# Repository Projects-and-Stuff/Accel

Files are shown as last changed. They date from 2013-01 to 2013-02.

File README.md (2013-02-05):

# Accel #
#### A 50cm diameter continuous pulsed solenoid for testing control and feedback algorithms ####
#### This can be considered to be a sort of infinite controlled coil gun or a miniature circular mass-driver ####
---

*File Structure*

* ./Firmware/ --> Firmware for the project (Written in C Utilizing AVR Studio 6)
* ./Hardware/ --> OpenSCAD part file and .STL file
* ./ElecHardware/ --> Kicad Projects for Accel
* ./GerberOutput/ --> The latest PCB Gerber Files for manufacture
* ./Notes/ --> Project Notes, BOM, and Research

---

Additional information, research, and notes can be found at http://www.projectsandstuff.com, or email us at support@projectsandstuff.com

Let us know if you fork and make improvements. We'd be glad to consider merges that improve this project.

---

Updates can be found in the Project Log, in the Notes folder

---

CURRENT AUTHORS:

> [Jack Linke](http://www.jacklinke.com)
jacklinke@gmail.com

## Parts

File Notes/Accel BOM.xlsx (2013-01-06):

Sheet: Control Board
Bill of Materials - Accel - Control Board |  |  |  |  |  |  |  |  |  | # of boards goal: | 1
Projects and Stuff LLC - http://www.projectsandstuff.com
Total BOM Parts Cost: | $1.23
Description | Mfg Part # | Package | KiCad Footprint | Default Supplier | Supplier On Hand | Qty per board | Total Qty Needed | Price per part at Qty | Total Price | Notes | Part References
Shift Register, 8-bit | MC74HC165ADG (http://www.digikey.com/product-detail/en/MC74HC165ADG/MC74HC165ADGOS-ND/1479887) | 16-SOIC |  | DigiKey | 8387 | 3 | 3 | $0.41000 | $1.23
 |  |  |  |  |  |  | 0 |  | $0.00
 |  |  |  |  |  |  | 0 |  | $0.00
 |  |  |  |  |  |  | 0 |  | $0.00
 |  |  |  |  |  |  | 0 |  | $0.00
 |  |  |  |  |  |  | 0 |  | $0.00
 |  |  |  |  |  |  | 0 |  | $0.00
 |  |  |  |  |  |  | 0 |  | $0.00
 |  |  |  |  |  |  | 0 |  | $0.00
 |  |  |  |  |  |  | 0 |  | $0.00
 |  |  |  |  |  |  | 0 |  | $0.00
 |  |  |  |  |  |  | 0 |  | $0.00
 |  |  |  |  |  |  | 0 |  | $0.00
 |  |  |  |  |  |  | 0 |  | $0.00
 |  |  |  |  |  |  | 0 |  | $0.00
 |  |  |  |  |  |  | 0 |  | $0.00
 |  |  |  |  |  |  | 0 |  | $0.00
 |  |  |  |  |  |  | 0 |  | $0.00
 |  |  |  |  |  |  | 0 |  | $0.00
 |  |  |  |  |  |  | 0 |  | $0.00
 |  |  |  |  |  |  | 0 |  | $0.00
 |  |  |  |  |  |  | 0 |  | $0.00
 |  |  |  |  |  |  | 0 |  | $0.00
 |  |  |  |  |  |  | 0 |  | $0.00
 |  |  |  |  |  |  | 0 |  | $0.00
 |  |  |  |  |  |  | 0 |  | $0.00
 |  |  |  |  |  |  | 0 |  | $0.00
 |  |  |  |  |  |  | 0 |  | $0.00
 |  |  |  |  |  |  | 0 |  | $0.00
 |  |  |  |  |  |  | 0 |  | $0.00
 |  |  |  |  |  |  | 0 |  | $0.00
 |  |  |  |  |  |  | 0 |  | $0.00
 |  |  |  |  |  |  | 0 |  | $0.00
 |  |  |  |  |  |  | 0 |  | $0.00
 |  |  |  |  |  |  | 0 |  | $0.00
 |  |  |  |  |  |  | 0 |  | $0.00
 |  |  |  |  |  |  | 0 |  | $0.00
 |  |  |  |  |  |  | 0 |  | $0.00
 |  |  |  |  |  |  | 0 |  | $0.00
 |  |  |  |  |  |  | 0 |  | $0.00
 |  |  |  |  |  |  | 0 |  | $0.00
 |  |  |  |  |  |  | 0 |  | $0.00
 |  |  |  |  |  |  | 0 |  | $0.00
 |  |  |  |  |  |  | 0 |  | $0.00
 |  |  |  |  |  |  | 0 |  | $0.00
 |  |  |  |  |  |  | 0 |  | $0.00
 |  |  |  |  |  |  | 0 |  | $0.00
 |  |  |  |  |  |  | 0 |  | $0.00
 |  |  |  |  |  |  | 0 |  | $0.00
 |  |  |  |  |  |  | 0 |  | $0.00
 |  |  |  |  |  |  | 0 |  | $0.00
 |  |  |  |  |  |  | 0 |  | $0.00
 |  |  |  |  |  |  | 0 |  | $0.00
 |  |  |  |  |  |  | 0 |  | $0.00
 |  |  |  |  |  |  | 0 |  | $0.00
 |  |  |  |  |  |  | 0 |  | $0.00
 |  |  |  |  |  |  | 0 |  | $0.00
 |  |  |  |  |  |  | 0 |  | $0.00
 |  |  |  |  |  |  | 0 |  | $0.00
 |  |  |  |  |  |  | 0 |  | $0.00
 |  |  |  |  |  |  | 0 |  | $0.00
 |  |  |  |  |  |  | 0 |  | $0.00
 |  |  |  |  |  |  | 0 |  | $0.00
 |  |  |  |  |  |  | 0 |  | $0.00
 |  |  |  |  |  |  | 0 |  | $0.00
 |  |  |  |  |  |  | 0 |  | $0.00
 |  |  |  |  |  |  | 0 |  | $0.00
 |  |  |  |  |  |  | 0 |  | $0.00
 |  |  |  |  |  |  | 0 |  | $0.00
 |  |  |  |  |  |  | 0 |  | $0.00
 |  |  |  |  |  |  | 0 |  | $0.00
 |  |  |  |  |  |  | 0 |  | $0.00
 |  |  |  |  |  |  | 0 |  | $0.00
 |  |  |  |  |  |  | 0 |  | $0.00
 |  |  |  |  |  |  | 0 |  | $0.00
 |  |  |  |  |  |  | 0 |  | $0.00
 |  |  |  |  |  |  | 0 |  | $0.00
 |  |  |  |  |  |  | 0 |  | $0.00
 |  |  |  |  |  |  | 0 |  | $0.00
 |  |  |  |  |  |  | 0 |  | $0.00
 |  |  |  |  |  |  | 0 |  | $0.00
 |  |  |  |  |  |  | 0 |  | $0.00
 |  |  |  |  |  |  | 0 |  | $0.00
 |  |  |  |  |  |  | 0 |  | $0.00
 |  |  |  |  |  |  | 0 |  | $0.00
 |  |  |  |  |  |  | 0 |  | $0.00
 |  |  |  |  |  |  | 0 |  | $0.00
 |  |  |  |  |  |  | 0 |  | $0.00
 |  |  |  |  |  |  | 0 |  | $0.00
 |  |  |  |  |  |  | 0 |  | $0.00
 |  |  |  |  |  |  | 0 |  | $0.00
 |  |  |  |  |  |  | 0 |  | $0.00
 |  |  |  |  |  |  | 0 |  | $0.00
 |  |  |  |  |  |  | 0 |  | $0.00
 |  |  |  |  |  |  | 0 |  | $0.00
 |  |  |  |  |  |  | 0 |  | $0.00
 |  |  |  |  |  |  | 0 |  | $0.00
 |  |  |  |  |  |  | 0 |  | $0.00
 |  |  |  |  |  |  | 0 |  | $0.00
 |  |  |  |  |  |  | 0 |  | $0.00
 |  |  |  |  |  |  | 0 |  | $0.00
 |  |  |  |  |  |  | 0 |  | $0.00
 |  |  |  |  |  |  | 0 |  | $0.00
 |  |  |  |  |  |  | 0 |  | $0.00
 |  |  |  |  |  |  | 0 |  | $0.00
 |  |  |  |  |  |  | 0 |  | $0.00
 |  |  |  |  |  |  | 0 |  | $0.00
 |  |  |  |  |  |  | 0 |  | $0.00
 |  |  |  |  |  |  | 0 |  | $0.00
 |  |  |  |  |  |  | 0 |  | $0.00
 |  |  |  |  |  |  | 0 |  | $0.00
 |  |  |  |  |  |  | 0 |  | $0.00
 |  |  |  |  |  |  | 0 |  | $0.00
 |  |  |  |  |  |  | 0 |  | $0.00
 |  |  |  |  |  |  | 0 |  | $0.00
 |  |  |  |  |  |  | 0 |  | $0.00
 |  |  |  |  |  |  | 0 |  | $0.00
 |  |  |  |  |  |  | 0 |  | $0.00
 |  |  |  |  |  |  | 0 |  | $0.00
 |  |  |  |  |  |  | 0 |  | $0.00
 |  |  |  |  |  |  | 0 |  | $0.00
 |  |  |  |  |  |  | 0 |  | $0.00
 |  |  |  |  |  |  | 0 |  | $0.00
 |  |  |  |  |  |  | 0 |  | $0.00
 |  |  |  |  |  |  | 0 |  | $0.00
 |  |  |  |  |  |  | 0 |  | $0.00
 |  |  |  |  |  |  | 0 |  | $0.00
 |  |  |  |  |  |  | 0 |  | $0.00
 |  |  |  |  |  |  | 0 |  | $0.00
 |  |  |  |  |  |  | 0 |  | $0.00
 |  |  |  |  |  |  | 0 |  | $0.00
 |  |  |  |  |  |  | 0 |  | $0.00
 |  |  |  |  |  |  | 0 |  | $0.00
 |  |  |  |  |  |  | 0 |  | $0.00
 |  |  |  |  |  |  | 0 |  | $0.00
 |  |  |  |  |  |  | 0 |  | $0.00
 |  |  |  |  |  |  | 0 |  | $0.00
 |  |  |  |  |  |  | 0 |  | $0.00
 |  |  |  |  |  |  | 0 |  | $0.00
 |  |  |  |  |  |  | 0 |  | $0.00
 |  |  |  |  |  |  | 0 |  | $0.00
 |  |  |  |  |  |  | 0 |  | $0.00
 |  |  |  |  |  |  | 0 |  | $0.00
 |  |  |  |  |  |  | 0 |  | $0.00
 |  |  |  |  |  |  | 0 |  | $0.00
 |  |  |  |  |  |  | 0 |  | $0.00
 |  |  |  |  |  |  | 0 |  | $0.00
 |  |  |  |  |  |  | 0 |  | $0.00
 |  |  |  |  |  |  | 0 |  | $0.00
 |  |  |  |  |  |  | 0 |  | $0.00
 |  |  |  |  |  |  | 0 |  | $0.00
 |  |  |  |  |  |  | 0 |  | $0.00
 |  |  |  |  |  |  | 0 |  | $0.00
 |  |  |  |  |  |  | 0 |  | $0.00
 |  |  |  |  |  |  | 0 |  | $0.00
 |  |  |  |  |  |  | 0 |  | $0.00
 |  |  |  |  |  |  | 0 |  | $0.00
 |  |  |  |  |  |  | 0 |  | $0.00
 |  |  |  |  |  |  | 0 |  | $0.00
 |  |  |  |  |  |  | 0 |  | $0.00
 |  |  |  |  |  |  | 0 |  | $0.00
 |  |  |  |  |  |  | 0 |  | $0.00
 |  |  |  |  |  |  | 0 |  | $0.00
 |  |  |  |  |  |  | 0 |  | $0.00
 |  |  |  |  |  |  | 0 |  | $0.00
 |  |  |  |  |  |  | 0 |  | $0.00
 |  |  |  |  |  |  | 0 |  | $0.00
 |  |  |  |  |  |  | 0 |  | $0.00
 |  |  |  |  |  |  | 0 |  | $0.00
 |  |  |  |  |  |  | 0 |  | $0.00
 |  |  |  |  |  |  | 0 |  | $0.00
 |  |  |  |  |  |  | 0 |  | $0.00
 |  |  |  |  |  |  | 0 |  | $0.00
 |  |  |  |  |  |  | 0 |  | $0.00
 |  |  |  |  |  |  | 0 |  | $0.00
 |  |  |  |  |  |  | 0 |  | $0.00
 |  |  |  |  |  |  | 0 |  | $0.00
 |  |  |  |  |  |  | 0 |  | $0.00
 |  |  |  |  |  |  | 0 |  | $0.00
 |  |  |  |  |  |  | 0 |  | $0.00
 |  |  |  |  |  |  | 0 |  | $0.00
 |  |  |  |  |  |  | 0 |  | $0.00
 |  |  |  |  |  |  | 0 |  | $0.00
 |  |  |  |  |  |  | 0 |  | $0.00
 |  |  |  |  |  |  | 0 |  | $0.00
 |  |  |  |  |  |  | 0 |  | $0.00
 |  |  |  |  |  |  | 0 |  | $0.00
 |  |  |  |  |  |  | 0 |  | $0.00
 |  |  |  |  |  |  | 0 |  | $0.00
 |  |  |  |  |  |  | 0 |  | $0.00
 |  |  |  |  |  |  | 0 |  | $0.00
 |  |  |  |  |  |  | 0 |  | $0.00
 |  |  |  |  |  |  | 0 |  | $0.00
 |  |  |  |  |  |  | 0 |  | $0.00
 |  |  |  |  |  |  | 0 |  | $0.00

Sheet: Phototransistor Board
Bill of Materials - Accel - Phototransistor Board |  |  |  |  |  |  |  |  |  | # of boards goal: | 24
Projects and Stuff LLC - http://www.projectsandstuff.com
Total BOM Parts Cost: | $10.28
Description | Mfg Part # | Package | KiCad Footprint | Default Supplier | Supplier On Hand | Qty per board | Total Qty Needed | Price per part at Qty | Total Price | Notes | Part References
Phototransistor | PT91-21B/TR7 (http://www.digikey.com/product-detail/en/PT91-21B%2FTR7/1080-1393-1-ND/2676127) | 2-SMD, Gull Wing |  | DigiKey | 3958 | 1 | 24 | $0.30200 | $7.25
Resistor 200 Ohm |  |  |  | DigiKey |  | 1 | 24 |  | $0.00
Resistor 510 Ohm |  |  |  | DigiKey |  | 1 | 24 |  | $0.00
Schmitt Trigger | SN74LVC1G17DBVR (http://www.digikey.com/product-detail/en/SN74LVC1G17DBVR/296-11933-1-ND/389050) | SOT-23-5 |  | DigiKey | 696000 | 1 | 24 | $0.12640 | $3.03
 |  |  |  |  |  |  | 0 |  | $0.00
 |  |  |  |  |  |  | 0 |  | $0.00
 |  |  |  |  |  |  | 0 |  | $0.00
 |  |  |  |  |  |  | 0 |  | $0.00
 |  |  |  |  |  |  | 0 |  | $0.00
 |  |  |  |  |  |  | 0 |  | $0.00
 |  |  |  |  |  |  | 0 |  | $0.00
 |  |  |  |  |  |  | 0 |  | $0.00
 |  |  |  |  |  |  | 0 |  | $0.00
 |  |  |  |  |  |  | 0 |  | $0.00
 |  |  |  |  |  |  | 0 |  | $0.00
 |  |  |  |  |  |  | 0 |  | $0.00
 |  |  |  |  |  |  | 0 |  | $0.00
 |  |  |  |  |  |  | 0 |  | $0.00
 |  |  |  |  |  |  | 0 |  | $0.00
 |  |  |  |  |  |  | 0 |  | $0.00
 |  |  |  |  |  |  | 0 |  | $0.00
 |  |  |  |  |  |  | 0 |  | $0.00
 |  |  |  |  |  |  | 0 |  | $0.00
 |  |  |  |  |  |  | 0 |  | $0.00
 |  |  |  |  |  |  | 0 |  | $0.00
 |  |  |  |  |  |  | 0 |  | $0.00
 |  |  |  |  |  |  | 0 |  | $0.00
 |  |  |  |  |  |  | 0 |  | $0.00
 |  |  |  |  |  |  | 0 |  | $0.00
 |  |  |  |  |  |  | 0 |  | $0.00
 |  |  |  |  |  |  | 0 |  | $0.00
 |  |  |  |  |  |  | 0 |  | $0.00
 |  |  |  |  |  |  | 0 |  | $0.00
 |  |  |  |  |  |  | 0 |  | $0.00
 |  |  |  |  |  |  | 0 |  | $0.00
 |  |  |  |  |  |  | 0 |  | $0.00
 |  |  |  |  |  |  | 0 |  | $0.00
 |  |  |  |  |  |  | 0 |  | $0.00
 |  |  |  |  |  |  | 0 |  | $0.00
 |  |  |  |  |  |  | 0 |  | $0.00
 |  |  |  |  |  |  | 0 |  | $0.00
 |  |  |  |  |  |  | 0 |  | $0.00
 |  |  |  |  |  |  | 0 |  | $0.00
 |  |  |  |  |  |  | 0 |  | $0.00
 |  |  |  |  |  |  | 0 |  | $0.00
 |  |  |  |  |  |  | 0 |  | $0.00
 |  |  |  |  |  |  | 0 |  | $0.00
 |  |  |  |  |  |  | 0 |  | $0.00
 |  |  |  |  |  |  | 0 |  | $0.00
 |  |  |  |  |  |  | 0 |  | $0.00
 |  |  |  |  |  |  | 0 |  | $0.00
 |  |  |  |  |  |  | 0 |  | $0.00
 |  |  |  |  |  |  | 0 |  | $0.00
 |  |  |  |  |  |  | 0 |  | $0.00
 |  |  |  |  |  |  | 0 |  | $0.00
 |  |  |  |  |  |  | 0 |  | $0.00
 |  |  |  |  |  |  | 0 |  | $0.00
 |  |  |  |  |  |  | 0 |  | $0.00
 |  |  |  |  |  |  | 0 |  | $0.00
 |  |  |  |  |  |  | 0 |  | $0.00
 |  |  |  |  |  |  | 0 |  | $0.00
 |  |  |  |  |  |  | 0 |  | $0.00
 |  |  |  |  |  |  | 0 |  | $0.00
 |  |  |  |  |  |  | 0 |  | $0.00
 |  |  |  |  |  |  | 0 |  | $0.00
 |  |  |  |  |  |  | 0 |  | $0.00
 |  |  |  |  |  |  | 0 |  | $0.00
 |  |  |  |  |  |  | 0 |  | $0.00
 |  |  |  |  |  |  | 0 |  | $0.00
 |  |  |  |  |  |  | 0 |  | $0.00
 |  |  |  |  |  |  | 0 |  | $0.00
 |  |  |  |  |  |  | 0 |  | $0.00
 |  |  |  |  |  |  | 0 |  | $0.00
 |  |  |  |  |  |  | 0 |  | $0.00
 |  |  |  |  |  |  | 0 |  | $0.00
 |  |  |  |  |  |  | 0 |  | $0.00
 |  |  |  |  |  |  | 0 |  | $0.00
 |  |  |  |  |  |  | 0 |  | $0.00
 |  |  |  |  |  |  | 0 |  | $0.00
 |  |  |  |  |  |  | 0 |  | $0.00
 |  |  |  |  |  |  | 0 |  | $0.00
 |  |  |  |  |  |  | 0 |  | $0.00
 |  |  |  |  |  |  | 0 |  | $0.00
 |  |  |  |  |  |  | 0 |  | $0.00
 |  |  |  |  |  |  | 0 |  | $0.00
 |  |  |  |  |  |  | 0 |  | $0.00
 |  |  |  |  |  |  | 0 |  | $0.00
 |  |  |  |  |  |  | 0 |  | $0.00
 |  |  |  |  |  |  | 0 |  | $0.00
 |  |  |  |  |  |  | 0 |  | $0.00
 |  |  |  |  |  |  | 0 |  | $0.00
 |  |  |  |  |  |  | 0 |  | $0.00
 |  |  |  |  |  |  | 0 |  | $0.00
 |  |  |  |  |  |  | 0 |  | $0.00
 |  |  |  |  |  |  | 0 |  | $0.00
 |  |  |  |  |  |  | 0 |  | $0.00
 |  |  |  |  |  |  | 0 |  | $0.00
 |  |  |  |  |  |  | 0 |  | $0.00
 |  |  |  |  |  |  | 0 |  | $0.00
 |  |  |  |  |  |  | 0 |  | $0.00
 |  |  |  |  |  |  | 0 |  | $0.00
 |  |  |  |  |  |  | 0 |  | $0.00
 |  |  |  |  |  |  | 0 |  | $0.00
 |  |  |  |  |  |  | 0 |  | $0.00
 |  |  |  |  |  |  | 0 |  | $0.00
 |  |  |  |  |  |  | 0 |  | $0.00
 |  |  |  |  |  |  | 0 |  | $0.00
 |  |  |  |  |  |  | 0 |  | $0.00
 |  |  |  |  |  |  | 0 |  | $0.00
 |  |  |  |  |  |  | 0 |  | $0.00
 |  |  |  |  |  |  | 0 |  | $0.00
 |  |  |  |  |  |  | 0 |  | $0.00
 |  |  |  |  |  |  | 0 |  | $0.00
 |  |  |  |  |  |  | 0 |  | $0.00
 |  |  |  |  |  |  | 0 |  | $0.00
 |  |  |  |  |  |  | 0 |  | $0.00
 |  |  |  |  |  |  | 0 |  | $0.00
 |  |  |  |  |  |  | 0 |  | $0.00
 |  |  |  |  |  |  | 0 |  | $0.00
 |  |  |  |  |  |  | 0 |  | $0.00
 |  |  |  |  |  |  | 0 |  | $0.00
 |  |  |  |  |  |  | 0 |  | $0.00
 |  |  |  |  |  |  | 0 |  | $0.00
 |  |  |  |  |  |  | 0 |  | $0.00
 |  |  |  |  |  |  | 0 |  | $0.00
 |  |  |  |  |  |  | 0 |  | $0.00
 |  |  |  |  |  |  | 0 |  | $0.00
 |  |  |  |  |  |  | 0 |  | $0.00
 |  |  |  |  |  |  | 0 |  | $0.00
 |  |  |  |  |  |  | 0 |  | $0.00
 |  |  |  |  |  |  | 0 |  | $0.00
 |  |  |  |  |  |  | 0 |  | $0.00
 |  |  |  |  |  |  | 0 |  | $0.00
 |  |  |  |  |  |  | 0 |  | $0.00
 |  |  |  |  |  |  | 0 |  | $0.00
 |  |  |  |  |  |  | 0 |  | $0.00
 |  |  |  |  |  |  | 0 |  | $0.00
 |  |  |  |  |  |  | 0 |  | $0.00
 |  |  |  |  |  |  | 0 |  | $0.00
 |  |  |  |  |  |  | 0 |  | $0.00
 |  |  |  |  |  |  | 0 |  | $0.00
 |  |  |  |  |  |  | 0 |  | $0.00
 |  |  |  |  |  |  | 0 |  | $0.00
 |  |  |  |  |  |  | 0 |  | $0.00
 |  |  |  |  |  |  | 0 |  | $0.00
 |  |  |  |  |  |  | 0 |  | $0.00
 |  |  |  |  |  |  | 0 |  | $0.00
 |  |  |  |  |  |  | 0 |  | $0.00
 |  |  |  |  |  |  | 0 |  | $0.00
 |  |  |  |  |  |  | 0 |  | $0.00
 |  |  |  |  |  |  | 0 |  | $0.00
 |  |  |  |  |  |  | 0 |  | $0.00
 |  |  |  |  |  |  | 0 |  | $0.00
 |  |  |  |  |  |  | 0 |  | $0.00
 |  |  |  |  |  |  | 0 |  | $0.00
 |  |  |  |  |  |  | 0 |  | $0.00
 |  |  |  |  |  |  | 0 |  | $0.00
 |  |  |  |  |  |  | 0 |  | $0.00
 |  |  |  |  |  |  | 0 |  | $0.00
 |  |  |  |  |  |  | 0 |  | $0.00
 |  |  |  |  |  |  | 0 |  | $0.00
 |  |  |  |  |  |  | 0 |  | $0.00
 |  |  |  |  |  |  | 0 |  | $0.00
 |  |  |  |  |  |  | 0 |  | $0.00
 |  |  |  |  |  |  | 0 |  | $0.00
 |  |  |  |  |  |  | 0 |  | $0.00
 |  |  |  |  |  |  | 0 |  | $0.00
 |  |  |  |  |  |  | 0 |  | $0.00
 |  |  |  |  |  |  | 0 |  | $0.00
 |  |  |  |  |  |  | 0 |  | $0.00
 |  |  |  |  |  |  | 0 |  | $0.00
 |  |  |  |  |  |  | 0 |  | $0.00
 |  |  |  |  |  |  | 0 |  | $0.00
 |  |  |  |  |  |  | 0 |  | $0.00
 |  |  |  |  |  |  | 0 |  | $0.00
 |  |  |  |  |  |  | 0 |  | $0.00
 |  |  |  |  |  |  | 0 |  | $0.00
 |  |  |  |  |  |  | 0 |  | $0.00
 |  |  |  |  |  |  | 0 |  | $0.00
 |  |  |  |  |  |  | 0 |  | $0.00
 |  |  |  |  |  |  | 0 |  | $0.00
 |  |  |  |  |  |  | 0 |  | $0.00
 |  |  |  |  |  |  | 0 |  | $0.00
 |  |  |  |  |  |  | 0 |  | $0.00
 |  |  |  |  |  |  | 0 |  | $0.00
 |  |  |  |  |  |  | 0 |  | $0.00
 |  |  |  |  |  |  | 0 |  | $0.00
 |  |  |  |  |  |  | 0 |  | $0.00
 |  |  |  |  |  |  | 0 |  | $0.00
 |  |  |  |  |  |  | 0 |  | $0.00
 |  |  |  |  |  |  | 0 |  | $0.00
 |  |  |  |  |  |  | 0 |  | $0.00
 |  |  |  |  |  |  | 0 |  | $0.00
 |  |  |  |  |  |  | 0 |  | $0.00
 |  |  |  |  |  |  | 0 |  | $0.00

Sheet: Emitter Board
Bill of Materials - Accel - Emitter Board |  |  |  |  |  |  |  |  |  | # of boards goal: | 24
Projects and Stuff LLC - http://www.projectsandstuff.com
Total BOM Parts Cost: | $8.45
Description | Mfg Part # | Package | KiCad Footprint | Default Supplier | Supplier On Hand | Qty per board | Total Qty Needed | Price per part at Qty | Total Price | Notes | Part References
LED, Infrared | IR95-21C/TR7 (http://www.digikey.com/product-detail/en/IR95-21C%2FTR7/1080-1364-1-ND/2676098) | 2-SMD, Gull Wing |  | DigiKey | 1595 | 1 | 24 | $0.35200 | $8.45
P-Type MOSFET |  |  |  |  |  |  | 0 |  | $0.00
 |  |  |  |  |  |  | 0 |  | $0.00
 |  |  |  |  |  |  | 0 |  | $0.00
 |  |  |  |  |  |  | 0 |  | $0.00
 |  |  |  |  |  |  | 0 |  | $0.00
 |  |  |  |  |  |  | 0 |  | $0.00
 |  |  |  |  |  |  | 0 |  | $0.00
 |  |  |  |  |  |  | 0 |  | $0.00
 |  |  |  |  |  |  | 0 |  | $0.00
 |  |  |  |  |  |  | 0 |  | $0.00
 |  |  |  |  |  |  | 0 |  | $0.00
 |  |  |  |  |  |  | 0 |  | $0.00
 |  |  |  |  |  |  | 0 |  | $0.00
 |  |  |  |  |  |  | 0 |  | $0.00
 |  |  |  |  |  |  | 0 |  | $0.00
 |  |  |  |  |  |  | 0 |  | $0.00
 |  |  |  |  |  |  | 0 |  | $0.00
 |  |  |  |  |  |  | 0 |  | $0.00
 |  |  |  |  |  |  | 0 |  | $0.00
 |  |  |  |  |  |  | 0 |  | $0.00
 |  |  |  |  |  |  | 0 |  | $0.00
 |  |  |  |  |  |  | 0 |  | $0.00
 |  |  |  |  |  |  | 0 |  | $0.00
 |  |  |  |  |  |  | 0 |  | $0.00
 |  |  |  |  |  |  | 0 |  | $0.00
 |  |  |  |  |  |  | 0 |  | $0.00
 |  |  |  |  |  |  | 0 |  | $0.00
 |  |  |  |  |  |  | 0 |  | $0.00
 |  |  |  |  |  |  | 0 |  | $0.00
 |  |  |  |  |  |  | 0 |  | $0.00
 |  |  |  |  |  |  | 0 |  | $0.00
 |  |  |  |  |  |  | 0 |  | $0.00
 |  |  |  |  |  |  | 0 |  | $0.00
 |  |  |  |  |  |  | 0 |  | $0.00
 |  |  |  |  |  |  | 0 |  | $0.00
 |  |  |  |  |  |  | 0 |  | $0.00
 |  |  |  |  |  |  | 0 |  | $0.00
 |  |  |  |  |  |  | 0 |  | $0.00
 |  |  |  |  |  |  | 0 |  | $0.00
 |  |  |  |  |  |  | 0 |  | $0.00
 |  |  |  |  |  |  | 0 |  | $0.00
 |  |  |  |  |  |  | 0 |  | $0.00
 |  |  |  |  |  |  | 0 |  | $0.00
 |  |  |  |  |  |  | 0 |  | $0.00
 |  |  |  |  |  |  | 0 |  | $0.00
 |  |  |  |  |  |  | 0 |  | $0.00
 |  |  |  |  |  |  | 0 |  | $0.00
 |  |  |  |  |  |  | 0 |  | $0.00
 |  |  |  |  |  |  | 0 |  | $0.00
 |  |  |  |  |  |  | 0 |  | $0.00
 |  |  |  |  |  |  | 0 |  | $0.00
 |  |  |  |  |  |  | 0 |  | $0.00
 |  |  |  |  |  |  | 0 |  | $0.00
 |  |  |  |  |  |  | 0 |  | $0.00
 |  |  |  |  |  |  | 0 |  | $0.00
 |  |  |  |  |  |  | 0 |  | $0.00
 |  |  |  |  |  |  | 0 |  | $0.00
 |  |  |  |  |  |  | 0 |  | $0.00
 |  |  |  |  |  |  | 0 |  | $0.00
 |  |  |  |  |  |  | 0 |  | $0.00
 |  |  |  |  |  |  | 0 |  | $0.00
 |  |  |  |  |  |  | 0 |  | $0.00
 |  |  |  |  |  |  | 0 |  | $0.00
 |  |  |  |  |  |  | 0 |  | $0.00
 |  |  |  |  |  |  | 0 |  | $0.00
 |  |  |  |  |  |  | 0 |  | $0.00
 |  |  |  |  |  |  | 0 |  | $0.00
 |  |  |  |  |  |  | 0 |  | $0.00
 |  |  |  |  |  |  | 0 |  | $0.00
 |  |  |  |  |  |  | 0 |  | $0.00
 |  |  |  |  |  |  | 0 |  | $0.00
 |  |  |  |  |  |  | 0 |  | $0.00
 |  |  |  |  |  |  | 0 |  | $0.00
 |  |  |  |  |  |  | 0 |  | $0.00
 |  |  |  |  |  |  | 0 |  | $0.00
 |  |  |  |  |  |  | 0 |  | $0.00
 |  |  |  |  |  |  | 0 |  | $0.00
 |  |  |  |  |  |  | 0 |  | $0.00
 |  |  |  |  |  |  | 0 |  | $0.00
 |  |  |  |  |  |  | 0 |  | $0.00
 |  |  |  |  |  |  | 0 |  | $0.00
 |  |  |  |  |  |  | 0 |  | $0.00
 |  |  |  |  |  |  | 0 |  | $0.00
 |  |  |  |  |  |  | 0 |  | $0.00
 |  |  |  |  |  |  | 0 |  | $0.00
 |  |  |  |  |  |  | 0 |  | $0.00
 |  |  |  |  |  |  | 0 |  | $0.00
 |  |  |  |  |  |  | 0 |  | $0.00
 |  |  |  |  |  |  | 0 |  | $0.00
 |  |  |  |  |  |  | 0 |  | $0.00
 |  |  |  |  |  |  | 0 |  | $0.00
 |  |  |  |  |  |  | 0 |  | $0.00
 |  |  |  |  |  |  | 0 |  | $0.00
 |  |  |  |  |  |  | 0 |  | $0.00
 |  |  |  |  |  |  | 0 |  | $0.00
 |  |  |  |  |  |  | 0 |  | $0.00
 |  |  |  |  |  |  | 0 |  | $0.00
 |  |  |  |  |  |  | 0 |  | $0.00
 |  |  |  |  |  |  | 0 |  | $0.00
 |  |  |  |  |  |  | 0 |  | $0.00
 |  |  |  |  |  |  | 0 |  | $0.00
 |  |  |  |  |  |  | 0 |  | $0.00
 |  |  |  |  |  |  | 0 |  | $0.00
 |  |  |  |  |  |  | 0 |  | $0.00
 |  |  |  |  |  |  | 0 |  | $0.00
 |  |  |  |  |  |  | 0 |  | $0.00
 |  |  |  |  |  |  | 0 |  | $0.00
 |  |  |  |  |  |  | 0 |  | $0.00
 |  |  |  |  |  |  | 0 |  | $0.00
 |  |  |  |  |  |  | 0 |  | $0.00
 |  |  |  |  |  |  | 0 |  | $0.00
 |  |  |  |  |  |  | 0 |  | $0.00
 |  |  |  |  |  |  | 0 |  | $0.00
 |  |  |  |  |  |  | 0 |  | $0.00
 |  |  |  |  |  |  | 0 |  | $0.00
 |  |  |  |  |  |  | 0 |  | $0.00
 |  |  |  |  |  |  | 0 |  | $0.00
 |  |  |  |  |  |  | 0 |  | $0.00
 |  |  |  |  |  |  | 0 |  | $0.00
 |  |  |  |  |  |  | 0 |  | $0.00
 |  |  |  |  |  |  | 0 |  | $0.00
 |  |  |  |  |  |  | 0 |  | $0.00
 |  |  |  |  |  |  | 0 |  | $0.00
 |  |  |  |  |  |  | 0 |  | $0.00
 |  |  |  |  |  |  | 0 |  | $0.00
 |  |  |  |  |  |  | 0 |  | $0.00
 |  |  |  |  |  |  | 0 |  | $0.00
 |  |  |  |  |  |  | 0 |  | $0.00
 |  |  |  |  |  |  | 0 |  | $0.00
 |  |  |  |  |  |  | 0 |  | $0.00
 |  |  |  |  |  |  | 0 |  | $0.00
 |  |  |  |  |  |  | 0 |  | $0.00
 |  |  |  |  |  |  | 0 |  | $0.00
 |  |  |  |  |  |  | 0 |  | $0.00
 |  |  |  |  |  |  | 0 |  | $0.00
 |  |  |  |  |  |  | 0 |  | $0.00
 |  |  |  |  |  |  | 0 |  | $0.00
 |  |  |  |  |  |  | 0 |  | $0.00
 |  |  |  |  |  |  | 0 |  | $0.00
 |  |  |  |  |  |  | 0 |  | $0.00
 |  |  |  |  |  |  | 0 |  | $0.00
 |  |  |  |  |  |  | 0 |  | $0.00
 |  |  |  |  |  |  | 0 |  | $0.00
 |  |  |  |  |  |  | 0 |  | $0.00
 |  |  |  |  |  |  | 0 |  | $0.00
 |  |  |  |  |  |  | 0 |  | $0.00
 |  |  |  |  |  |  | 0 |  | $0.00
 |  |  |  |  |  |  | 0 |  | $0.00
 |  |  |  |  |  |  | 0 |  | $0.00
 |  |  |  |  |  |  | 0 |  | $0.00
 |  |  |  |  |  |  | 0 |  | $0.00
 |  |  |  |  |  |  | 0 |  | $0.00
 |  |  |  |  |  |  | 0 |  | $0.00
 |  |  |  |  |  |  | 0 |  | $0.00
 |  |  |  |  |  |  | 0 |  | $0.00
 |  |  |  |  |  |  | 0 |  | $0.00
 |  |  |  |  |  |  | 0 |  | $0.00
 |  |  |  |  |  |  | 0 |  | $0.00
 |  |  |  |  |  |  | 0 |  | $0.00
 |  |  |  |  |  |  | 0 |  | $0.00
 |  |  |  |  |  |  | 0 |  | $0.00
 |  |  |  |  |  |  | 0 |  | $0.00
 |  |  |  |  |  |  | 0 |  | $0.00
 |  |  |  |  |  |  | 0 |  | $0.00
 |  |  |  |  |  |  | 0 |  | $0.00
 |  |  |  |  |  |  | 0 |  | $0.00
 |  |  |  |  |  |  | 0 |  | $0.00
 |  |  |  |  |  |  | 0 |  | $0.00
 |  |  |  |  |  |  | 0 |  | $0.00
 |  |  |  |  |  |  | 0 |  | $0.00
 |  |  |  |  |  |  | 0 |  | $0.00
 |  |  |  |  |  |  | 0 |  | $0.00
 |  |  |  |  |  |  | 0 |  | $0.00
 |  |  |  |  |  |  | 0 |  | $0.00
 |  |  |  |  |  |  | 0 |  | $0.00
 |  |  |  |  |  |  | 0 |  | $0.00
 |  |  |  |  |  |  | 0 |  | $0.00
 |  |  |  |  |  |  | 0 |  | $0.00
 |  |  |  |  |  |  | 0 |  | $0.00
 |  |  |  |  |  |  | 0 |  | $0.00
 |  |  |  |  |  |  | 0 |  | $0.00
 |  |  |  |  |  |  | 0 |  | $0.00
 |  |  |  |  |  |  | 0 |  | $0.00
 |  |  |  |  |  |  | 0 |  | $0.00
 |  |  |  |  |  |  | 0 |  | $0.00
 |  |  |  |  |  |  | 0 |  | $0.00
 |  |  |  |  |  |  | 0 |  | $0.00
 |  |  |  |  |  |  | 0 |  | $0.00
 |  |  |  |  |  |  | 0 |  | $0.00
 |  |  |  |  |  |  | 0 |  | $0.00
 |  |  |  |  |  |  | 0 |  | $0.00
 |  |  |  |  |  |  | 0 |  | $0.00
 |  |  |  |  |  |  | 0 |  | $0.00
 |  |  |  |  |  |  | 0 |  | $0.00

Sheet: Other
Bill of Materials - Accel - Other |  |  |  |  |  |  |  | # of boards goal: | 1000
Projects and Stuff LLC - http://www.projectsandstuff.com
Total BOM Parts Cost: | $0.00
Description | Mfg Part # | Default Supplier | Supplier On Hand | Qty per board | Total Qty Needed | Price per part at Qty | Total Price | Notes | Part References
 |  |  |  |  | 0 |  | $0.00
 |  |  |  |  | 0 |  | $0.00
 |  |  |  |  | 0 |  | $0.00
 |  |  |  |  | 0 |  | $0.00
 |  |  |  |  | 0 |  | $0.00
 |  |  |  |  | 0 |  | $0.00
 |  |  |  |  | 0 |  | $0.00
 |  |  |  |  | 0 |  | $0.00
 |  |  |  |  | 0 |  | $0.00
 |  |  |  |  | 0 |  | $0.00
 |  |  |  |  | 0 |  | $0.00
 |  |  |  |  | 0 |  | $0.00
 |  |  |  |  | 0 |  | $0.00
 |  |  |  |  | 0 |  | $0.00
 |  |  |  |  | 0 |  | $0.00
 |  |  |  |  | 0 |  | $0.00
 |  |  |  |  | 0 |  | $0.00
 |  |  |  |  | 0 |  | $0.00
 |  |  |  |  | 0 |  | $0.00
 |  |  |  |  | 0 |  | $0.00
 |  |  |  |  | 0 |  | $0.00
 |  |  |  |  | 0 |  | $0.00
 |  |  |  |  | 0 |  | $0.00
 |  |  |  |  | 0 |  | $0.00
 |  |  |  |  | 0 |  | $0.00
 |  |  |  |  | 0 |  | $0.00
 |  |  |  |  | 0 |  | $0.00
 |  |  |  |  | 0 |  | $0.00
 |  |  |  |  | 0 |  | $0.00
 |  |  |  |  | 0 |  | $0.00
 |  |  |  |  | 0 |  | $0.00
 |  |  |  |  | 0 |  | $0.00
 |  |  |  |  | 0 |  | $0.00
 |  |  |  |  | 0 |  | $0.00
 |  |  |  |  | 0 |  | $0.00
 |  |  |  |  | 0 |  | $0.00
 |  |  |  |  | 0 |  | $0.00
 |  |  |  |  | 0 |  | $0.00
 |  |  |  |  | 0 |  | $0.00
 |  |  |  |  | 0 |  | $0.00
 |  |  |  |  | 0 |  | $0.00
 |  |  |  |  | 0 |  | $0.00
 |  |  |  |  | 0 |  | $0.00
 |  |  |  |  | 0 |  | $0.00
 |  |  |  |  | 0 |  | $0.00
 |  |  |  |  | 0 |  | $0.00
 |  |  |  |  | 0 |  | $0.00
 |  |  |  |  | 0 |  | $0.00
 |  |  |  |  | 0 |  | $0.00
 |  |  |  |  | 0 |  | $0.00
 |  |  |  |  | 0 |  | $0.00
 |  |  |  |  | 0 |  | $0.00
 |  |  |  |  | 0 |  | $0.00
 |  |  |  |  | 0 |  | $0.00
 |  |  |  |  | 0 |  | $0.00
 |  |  |  |  | 0 |  | $0.00
 |  |  |  |  | 0 |  | $0.00
 |  |  |  |  | 0 |  | $0.00
 |  |  |  |  | 0 |  | $0.00
 |  |  |  |  | 0 |  | $0.00
 |  |  |  |  | 0 |  | $0.00
 |  |  |  |  | 0 |  | $0.00
 |  |  |  |  | 0 |  | $0.00
 |  |  |  |  | 0 |  | $0.00
 |  |  |  |  | 0 |  | $0.00
 |  |  |  |  | 0 |  | $0.00
 |  |  |  |  | 0 |  | $0.00
 |  |  |  |  | 0 |  | $0.00
 |  |  |  |  | 0 |  | $0.00
 |  |  |  |  | 0 |  | $0.00
 |  |  |  |  | 0 |  | $0.00
 |  |  |  |  | 0 |  | $0.00
 |  |  |  |  | 0 |  | $0.00
 |  |  |  |  | 0 |  | $0.00
 |  |  |  |  | 0 |  | $0.00
 |  |  |  |  | 0 |  | $0.00
 |  |  |  |  | 0 |  | $0.00
 |  |  |  |  | 0 |  | $0.00
 |  |  |  |  | 0 |  | $0.00
 |  |  |  |  | 0 |  | $0.00
 |  |  |  |  | 0 |  | $0.00
 |  |  |  |  | 0 |  | $0.00
 |  |  |  |  | 0 |  | $0.00
 |  |  |  |  | 0 |  | $0.00
 |  |  |  |  | 0 |  | $0.00
 |  |  |  |  | 0 |  | $0.00
 |  |  |  |  | 0 |  | $0.00
 |  |  |  |  | 0 |  | $0.00
 |  |  |  |  | 0 |  | $0.00
 |  |  |  |  | 0 |  | $0.00
 |  |  |  |  | 0 |  | $0.00
 |  |  |  |  | 0 |  | $0.00
 |  |  |  |  | 0 |  | $0.00
 |  |  |  |  | 0 |  | $0.00
 |  |  |  |  | 0 |  | $0.00
 |  |  |  |  | 0 |  | $0.00
 |  |  |  |  | 0 |  | $0.00
 |  |  |  |  | 0 |  | $0.00
 |  |  |  |  | 0 |  | $0.00
 |  |  |  |  | 0 |  | $0.00
 |  |  |  |  | 0 |  | $0.00
 |  |  |  |  | 0 |  | $0.00
 |  |  |  |  | 0 |  | $0.00
 |  |  |  |  | 0 |  | $0.00
 |  |  |  |  | 0 |  | $0.00
 |  |  |  |  | 0 |  | $0.00
 |  |  |  |  | 0 |  | $0.00
 |  |  |  |  | 0 |  | $0.00
 |  |  |  |  | 0 |  | $0.00
 |  |  |  |  | 0 |  | $0.00
 |  |  |  |  | 0 |  | $0.00
 |  |  |  |  | 0 |  | $0.00
 |  |  |  |  | 0 |  | $0.00
 |  |  |  |  | 0 |  | $0.00
 |  |  |  |  | 0 |  | $0.00
 |  |  |  |  | 0 |  | $0.00
 |  |  |  |  | 0 |  | $0.00
 |  |  |  |  | 0 |  | $0.00
 |  |  |  |  | 0 |  | $0.00
 |  |  |  |  | 0 |  | $0.00
 |  |  |  |  | 0 |  | $0.00
 |  |  |  |  | 0 |  | $0.00
 |  |  |  |  | 0 |  | $0.00
 |  |  |  |  | 0 |  | $0.00
 |  |  |  |  | 0 |  | $0.00
 |  |  |  |  | 0 |  | $0.00
 |  |  |  |  | 0 |  | $0.00
 |  |  |  |  | 0 |  | $0.00
 |  |  |  |  | 0 |  | $0.00
 |  |  |  |  | 0 |  | $0.00
 |  |  |  |  | 0 |  | $0.00
 |  |  |  |  | 0 |  | $0.00
 |  |  |  |  | 0 |  | $0.00
 |  |  |  |  | 0 |  | $0.00
 |  |  |  |  | 0 |  | $0.00
 |  |  |  |  | 0 |  | $0.00
 |  |  |  |  | 0 |  | $0.00
 |  |  |  |  | 0 |  | $0.00
 |  |  |  |  | 0 |  | $0.00
 |  |  |  |  | 0 |  | $0.00
 |  |  |  |  | 0 |  | $0.00
 |  |  |  |  | 0 |  | $0.00
 |  |  |  |  | 0 |  | $0.00
 |  |  |  |  | 0 |  | $0.00
 |  |  |  |  | 0 |  | $0.00
 |  |  |  |  | 0 |  | $0.00
 |  |  |  |  | 0 |  | $0.00
 |  |  |  |  | 0 |  | $0.00
 |  |  |  |  | 0 |  | $0.00
 |  |  |  |  | 0 |  | $0.00
 |  |  |  |  | 0 |  | $0.00
 |  |  |  |  | 0 |  | $0.00
 |  |  |  |  | 0 |  | $0.00
 |  |  |  |  | 0 |  | $0.00
 |  |  |  |  | 0 |  | $0.00
 |  |  |  |  | 0 |  | $0.00
 |  |  |  |  | 0 |  | $0.00
 |  |  |  |  | 0 |  | $0.00
 |  |  |  |  | 0 |  | $0.00
 |  |  |  |  | 0 |  | $0.00
 |  |  |  |  | 0 |  | $0.00
 |  |  |  |  | 0 |  | $0.00
 |  |  |  |  | 0 |  | $0.00
 |  |  |  |  | 0 |  | $0.00
 |  |  |  |  | 0 |  | $0.00
 |  |  |  |  | 0 |  | $0.00
 |  |  |  |  | 0 |  | $0.00
 |  |  |  |  | 0 |  | $0.00
 |  |  |  |  | 0 |  | $0.00
 |  |  |  |  | 0 |  | $0.00
 |  |  |  |  | 0 |  | $0.00
 |  |  |  |  | 0 |  | $0.00
 |  |  |  |  | 0 |  | $0.00
 |  |  |  |  | 0 |  | $0.00
 |  |  |  |  | 0 |  | $0.00
 |  |  |  |  | 0 |  | $0.00
 |  |  |  |  | 0 |  | $0.00
 |  |  |  |  | 0 |  | $0.00
 |  |  |  |  | 0 |  | $0.00
 |  |  |  |  | 0 |  | $0.00
 |  |  |  |  | 0 |  | $0.00
 |  |  |  |  | 0 |  | $0.00
 |  |  |  |  | 0 |  | $0.00
 |  |  |  |  | 0 |  | $0.00
 |  |  |  |  | 0 |  | $0.00
 |  |  |  |  | 0 |  | $0.00
 |  |  |  |  | 0 |  | $0.00
 |  |  |  |  | 0 |  | $0.00
 |  |  |  |  | 0 |  | $0.00
 |  |  |  |  | 0 |  | $0.00
 |  |  |  |  | 0 |  | $0.00
 |  |  |  |  | 0 |  | $0.00
 |  |  |  |  | 0 |  | $0.00
 |  |  |  |  | 0 |  | $0.00
 |  |  |  |  | 0 |  | $0.00

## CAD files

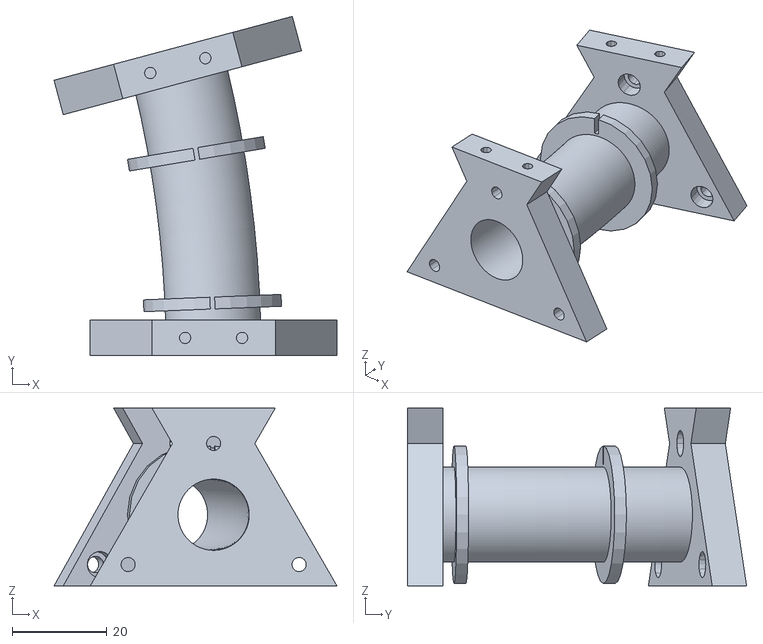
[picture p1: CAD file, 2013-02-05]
Hardware/3D Parts/Segment.stl
59.6 x 71.4 x 37.5

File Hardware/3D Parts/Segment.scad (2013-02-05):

//Create Outer Tube and subtract inner tube and limit entire thing to 15 degrees
difference() {



	union() {
	
		//Outer Tube
		rotate_extrude(convexity = 10, $fn = 240)
		translate([250, 0, 0])
		circle(r = 10, $fn = 100);



	// Create the Standard End
	translate([250, 0, 0]){
		difference() {
			union() { // Combine the two triangles
				// Triangular Portion
				rotate(a=90, v=[0,0,90]) {
					rotate(a=180, v=[1,0,0]) {
						rotate(a=90, v=[0,1,0]) {
							cylinder(h = 7.5, r=30, $fn=3);
						}
					}
				}
				
				// Upside Down Triangular Portion
				translate([0, 0, 14.95]){
					rotate(a=90, v=[0,0,1]) {
						rotate(a=0, v=[1,0,0]) {
							rotate(a=90, v=[0,1,0]) {
								cylinder(h = 7.5, r=15, $fn=3);
							}
						}
					}	
				}
				
				
				
				
			}

			// Top Cut-off
				translate([0, 0, 25]){
					rotate(a=90, v=[0,0,90]) {
						rotate(a=180, v=[1,0,0]) {
							rotate(a=90, v=[0,1,0]) {
								cylinder(h = 7.6, r=5.1, $fn=3);
							}
						}
					}
				}
			
			// Bottom Screw Holes
				translate([0, 0, -15.1]){ // Move cylinder to bottom of triangular end
					translate([0, 3.73, 0]){ // Move cylinder to middle width-wise
						translate([11.5, 0, 0]){ // Move cylinder toward traingle corner
							cylinder(h = 12.1, r=2.25, $fn=18); 
						}
					}
				}
				translate([0, 0, -15.1]){ // Move cylinder to bottom of triangular end
					translate([0, 3.73, 0]){ // Move cylinder to middle width-wise
						translate([-11.5, 0, 0]){ // Move cylinder toward traingle corner
							cylinder(h = 12.1, r=2.25, $fn=18); 
						}
					}
				}
				
			// Top Screw Holes
				translate([0, 0, 15.5]){ // Move cylinder to bottom of triangular end
					translate([0, 3.73, 0]){ // Move cylinder to middle width-wise
						translate([6, 0, 0]){ // Move cylinder toward traingle corner
							cylinder(h = 7, r=1.2, $fn=18); 
						}
					}
				}
				translate([0, 0, 15.5]){ // Move cylinder to bottom of triangular end
					translate([0, 3.73, 0]){ // Move cylinder to middle width-wise
						translate([-6, 0, 0]){ // Move cylinder toward traingle corner
							cylinder(h = 7, r=1.2, $fn=18); 
						}
					}
				}

			// Side Screw Holes (Smaller to actually screw in)
				rotate(a=90, v=[1,0,0]) { // TOP Screw Hole
					translate([0, 0, -8]){ // Move along Y
						translate([0, 15, 0]){ // Move along Z
							translate([0, 0, 0]){ // Move along X
								cylinder(h = 8.5, r=1.5, $fn=18); 
							}
						}
					}
				}
				rotate(a=90, v=[1,0,0]) {
					translate([0, 0, -8]){ // Move along Y
						translate([0, -10.5, 0]){ // Move along Z
							translate([18, 0, 0]){ // Move along X
								cylinder(h = 8.5, r=1.5, $fn=18); 
							}
						}
					}
				}
				rotate(a=90, v=[1,0,0]) {
					translate([0, 0, -8]){ // Move along Y
						translate([0, -10.5, 0]){ // Move along Z
							translate([-18, 0, 0]){ // Move along X
								cylinder(h = 8.5, r=1.5, $fn=18); 
							}
						}
					}
				}
			
			}
	}




	// Create the Rotated End
	rotate(a=15, v=[0,0,1]) {
		translate([250, 0, 0]){
					
			translate([0, -7.5, 0]){
				difference() {
					union() { // Combine the two triangles
						// Triangular Portion
						rotate(a=90, v=[0,0,90]) {
							rotate(a=180, v=[1,0,0]) {
								rotate(a=90, v=[0,1,0]) {
									cylinder(h = 7.5, r=30, $fn=3);
								}
							}
						}
						
						// Upside Down Triangular Portion
						translate([0, 0, 14.95]){
							rotate(a=90, v=[0,0,1]) {
								rotate(a=0, v=[1,0,0]) {
									rotate(a=90, v=[0,1,0]) {
										cylinder(h = 7.5, r=15, $fn=3);
									}
								}
							}	
						}
						
					}

					// Top Cut-off
						translate([0, 0, 25]){
							rotate(a=90, v=[0,0,90]) {
								rotate(a=180, v=[1,0,0]) {
									rotate(a=90, v=[0,1,0]) {
										cylinder(h = 7.6, r=5.1, $fn=3);
									}
								}
							}
						}
					
					// Bottom Screw Holes
						translate([0, 0, -15.1]){ // Move cylinder to bottom of triangular end
							translate([0, 3.73, 0]){ // Move cylinder to middle width-wise
								translate([11.5, 0, 0]){ // Move cylinder toward traingle corner
									cylinder(h = 12.1, r=2.25, $fn=18); 
								}
							}
						}
						translate([0, 0, -15.1]){ // Move cylinder to bottom of triangular end
							translate([0, 3.73, 0]){ // Move cylinder to middle width-wise
								translate([-11.5, 0, 0]){ // Move cylinder toward traingle corner
									cylinder(h = 12.1, r=2.25, $fn=18); 
								}
							}
						}
				
					// Top Screw Holes
						translate([0, 0, 15.5]){ // Move cylinder to bottom of triangular end
							translate([0, 3.73, 0]){ // Move cylinder to middle width-wise
								translate([6, 0, 0]){ // Move cylinder toward traingle corner
									cylinder(h = 7, r=1.2, $fn=18); 
								}
							}
						}
						translate([0, 0, 15.5]){ // Move cylinder to bottom of triangular end
							translate([0, 3.73, 0]){ // Move cylinder to middle width-wise
								translate([-6, 0, 0]){ // Move cylinder toward traingle corner
									cylinder(h = 7, r=1.2, $fn=18); 
								}
							}
						}

					// Side Screw Holes (Larger for free movement)
						rotate(a=90, v=[1,0,0]) { // TOP Screw Hole
							translate([0, 0, -8]){ // Move along Y
								translate([0, 15, 0]){ // Move along Z
									translate([0, 0, 0]){ // Move along X
										cylinder(h = 8.5, r=1.75, $fn=18); 
									}
								}
							}
						}
						rotate(a=90, v=[1,0,0]) {
							translate([0, 0, -8]){ // Move along Y
								translate([0, -10.5, 0]){ // Move along Z
									translate([18, 0, 0]){ // Move along X
										cylinder(h = 8.5, r=1.75, $fn=18); 
									}
								}
							}
						}
						rotate(a=90, v=[1,0,0]) {
							translate([0, 0, -8]){ // Move along Y
								translate([0, -10.5, 0]){ // Move along Z
									translate([-18, 0, 0]){ // Move along X
										cylinder(h = 8.5, r=1.75, $fn=18); 
									}
								}
							}
						}
					

					// Side Screw Holes (Countersink)
						rotate(a=90, v=[1,0,0]) {
							translate([0, 0, -3.5]){ // Move along Y
								translate([0, 15, 0]){ // Move along Z
									translate([0, 0, 0]){ // Move along X
										cylinder(h = 4, r=2.75, $fn=18); 
									}
								}
							}
						}
						rotate(a=90, v=[1,0,0]) {
							translate([0, 0, -3.5]){ // Move along Y
								translate([0, -10.5, 0]){ // Move along Z
									translate([18, 0, 0]){ // Move along X
										cylinder(h = 4, r=2.75, $fn=18); 
									}
								}
							}
						}
						rotate(a=90, v=[1,0,0]) {
							translate([0, 0, -3.5]){ // Move along Y
								translate([0, -10.5, 0]){ // Move along Z
									translate([-18, 0, 0]){ // Move along X
										cylinder(h = 4, r=2.75, $fn=18); 
									}
								}
							}
						}
					
					}
				}
				
			}
		}

		
		
// Ring 1
	rotate(a=9.5, v=[0,0,1]) { // How far (between 0 and 15 degrees) do we rotate the ring?
		translate([250, 0, 0]){
			difference() {

				rotate(a=90, v=[0,0,90]) {
					rotate(a=180, v=[1,0,0]) {
						rotate(a=90, v=[0,1,0]) {
							cylinder(h = 2.5, r=14.5, $fn=24);
						}
					}
				}

				translate(v = [0, 1.5, 12.6]) {
					cube(size = [1,3.2,4], center = true);
				}

			}
		}
	}
	
	
// Ring 2
	rotate(a=2.25, v=[0,0,1]) { // How far (between 0 and 15 degrees) do we rotate the ring?
		translate([250, 0, 0]){
			difference() {

				rotate(a=90, v=[0,0,90]) {
					rotate(a=180, v=[1,0,0]) {
						rotate(a=90, v=[0,1,0]) {
							cylinder(h = 2.5, r=14.5, $fn=24);
						}
					}
				}

				translate(v = [0, 1.5, 12.6]) {
					cube(size = [1,3.2,4], center = true);
				}

			}
		}
	}
	
		

	}		






	// Inner tube
	rotate_extrude(convexity = 10, $fn = 240)
	translate([250, 0, 0])
	circle(r = 7.5, $fn = 100);
	
	// Create the 15 degree section
	translate([0, 0, -10]){
		rotate(a = 15){	
			cube(size = [300,300,20], center = false);
		}
	}

	// Cut away the remainder of the ring
	for(i=[90:90:270]){
		translate([0, 0, -10]){
			rotate(i){	
				cube(size = [300,300,20], center = false);
			}
		}
	}


}
	

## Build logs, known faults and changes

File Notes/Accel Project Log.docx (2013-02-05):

Projects and Stuff

Accel

Project Log

# 2012/10/03

This evening I created the initial git repository, and began sketching out initial plans.

I’ll be using Google Sketchup to build most components in this project.

Initial notes:

Ring Radius: 500 mm

Ring Diameter: 1000 mm

(Ring dimensions are drawn to the center of the tube)

Ring Segment central angle: 18 degrees

Total Segments: 20

Ring Segment Arc Length (at center of tube): ~157.0796326794897 mm

Ring Total Circumference: ~3141.592653589793 mm

Tube diameter: 27.4 mm

Tube Thickness: 5.0 mm

Remember to include on each segment:

- Wire guides

- Sensor mountings (LED/magnetic/etc)

- Assembly (3-4 screw posts/holes at each tube end)

- Stand mounts for securing to a surface (closer to surface = better)

Also consider foam dampers at mount points, and a heavy base is best

Consider placing a cheap ADC or Schmitt Trigger along with each sensor to get quick, accurate results back to the main board quickly.

Alternately, use a (Optical - Photo Detectors - Logic Output) as a simple and possibly cheaper solution.

The following math isn't 100% accurate, because I'm calculating it for the center of the tube, but it's near enough not to matter:

My magnet will be 1 inch in diameter, and 1 inch in length. 1 inch is equal to 25.4 mm

With a ring radius of 500 mm, a central angle of 2.91 degrees gives an arc length of 25.4 mm. Expanding with some basic trig, the segment height - essentially the additional tolerance needed in the tube radius to allow the magnet to pass smoothly - is 0.16 mm. For the sake of simplicity, and to provide just a bit of additional tolerance in case of manufacturing imperfections, I'll use an inner diameter of 27.4 mm, well beyond what should be required if everything were ideal. We'll use a wall thickness of 5 mm.

# 2012/12/16

The past couple months have been pretty busy, so while I haven’t made many updates here, I’ve been working furiously on this and other projects. I’ll attempt to catch up here.

In order to reduce costs, I’ve made a design decision to reduce the diameter from 1 meter to 50cm. This also means that the projectile will now be half the original size (~12.7mm), and so the inner tube will also be smaller (~15mm)

I’m going to post the initial Sketchup model for the first coil section prototype and push to GitHub. Then I’ll continue updates here.

I printed the uploaded model on a 3D Touch 3D printer, using natural PLA plastic. I then used 22 AWG wire and coiled 3 layers of wire. I secured it in place with some enamel and tape, and performed some very basic tests between 10 and 24 volts.

The circumference of the entire circle (from the center of the tube) is 1570.79 mm. We’ll round to 1570 mm. I decided 24 segments of 15 degrees each makes more sense. 157/24 = ~65.42 mm. For simplicity we’ll approximate to 65.5 mm. This makes the final circumference (from tube center) 1572 mm, which is ~1.2 mm off from the ideal. This will work just fine.

The length of the segment will be as follows:

End 6 mm

Spacer 4 mm

Coil 25.5 mm

Sensor/Gap 20 mm

Spacer 4 mm

End 6 mm

# 2013/01/01

Uploaded the progress from the past week. I created a new prototype 15-degree segment, including the bend. I’m quickly improving in my abilities to effectively use Sketchup, and am implementing better processes as I learn.

The most recent prototype didn’t print out as nicely as the previous one, and some changes are still required, including larger holes in the bottom.

Here are the latest notes and measurements for the segments:

24 segments of 15 degrees each

65.5 mm Length (through center tube)

1572 mm Total Length (through center hole)

Lengthwise Measurements:

End 07.50 mm

Spacing 03.00 mm

Ring 03.00 mm

Coil 26.50 mm

Ring 03.00 mm

Sensor/Gap 15.00 mm

End 07.50 mm

Other Measurements:

Inner Tube Radius 07.50 mm

Outer Tube Radius 10.00 mm

Ring Radius 14.50 mm

End Inradius 15.00 mm

End Top Bevel 10.00 mm

Bottom Screws XX.XX mm (Actual thread size for 8-32 screw)

End Screws 02.00 mm

End Apothem 30.00 mm

Arc Height 02.14 mm

I still need to determine a number of things to proceed:

- What size screws to use on to hold the ends together, and to secure them to a base?
- How to secure the sensors (and related boards) to the segments?
- Should the tube thickness be increased further in order to facilitate better sensor placement?
- Should I use two curves in Sketchup, rather than a circle, when creating the inner tube? This might prevent the stretching I’ve seen in the latest prototype.

# 2013/01/05

In building the next version of the segment prototypes, for the inner radius I used 2 curves with a radius of 7.5 mm and a width of 7.25 mm, creating a pseudo-ellipse 15 mm by 14.5 mm. This is because when we eventually curve the tube, it will widen as part of the transform. If we used a 15 mm circle instead of two thinner curves, we end up with a tube that's more than 15 mm wide. I then did the same with the outer radius of the tube.

For the screws holding the segments to the base, I’ll use 8-32 screws, ¾” long. The base material will be ½” (approx. 12.7 mm) thick, and the screw heads are 4 mm, so I’ll counter-sink 4 mm into the base material. This means approximately 8.7 mm of threaded screw length will be going into the bottom of the segments. I’ll round up to 10mm. I’m using an 8-32 screw model, provided by Google, to create the holes using the solid modeling tools.

I will be using X-XX screws ½” (12.7 mm) to hold the segments together. Because this screw is so small in diameter compared to the thickness of the part, I will simply make simple 2 mm holes.

The screw holes must be added after the 3D part has been bent, so that the screw holes are not deformed.

For the sensors, I have decided to use infrared emitting LEDs and infrared phototransistors. The plan is to use 3 parallel-to-serial shift registers (74HC165) to clock the status of all 24 segment sensors into the microcontroller so that we’ll be able to see the status of all 24 sensors at a given instant.

On the Phototransistor Board, we’re using a common-emitter configuration, since we’re most concerned with voltage (as the input to the Schmitt trigger), and not current. The Collector-Emitter Saturation Voltage is 0.4 V. Max current for the device is 20 mA.

Collector Resistor: (VCC – ½VCC) / I

(5 – 2.5) / 0.005 = 500 Ohms

Emitter Resistor: VE / I

1V / 0.005 = 200 Ohms

# 2013/02/04

I have made a huge amount of progress over the past couple weeks, and haven’t done very well on documenting. I’ll attempt to go back over some of the changes.

The first three prototypes were designed in Sketchup. While I had a lot of success using this method, I had four distinct concerns:

- While the program is easy to use, it is not open source, and STL exports require either the Pro version or potentially buggy plug-ins.
- I had to design each prototype from scratch. While it became easier as I repeated steps with each prototype, I couldn’t just go back and make a simple change.
- Sketchup is not designed for making precision parts. It was primarily created as a method of roughing out architecture, and while it has improved significantly, it’s not the best tool for the job I’m working on.
- The tool I was using to bend the segments distorted the inner and outer tubes, requiring me to use curves to arrive at a final product that would be approximately round.

For the next prototypes, I used OpenSCAD. While somewhat of a memory hog, OpenSCAD allows me to make very precise parts. And because parts are designed programmatically, I can make changes anywhere on the part at any time.

In prototype 3 I accidentally countersunk holes in the wrong side of the ends. I have corrected this in prototype 4.

Prototype 5 includes a flat top to the segment, which allows for the installation of a printed circuit board. This board will perform the following functions:

- Turn sensors on or off, depending on instructions from the master control board
- Process and return sensor data to master control board
- Turn the coil on and off in either direction
- Sense coil temperature, turning on a fan when any coil is too hot

Clearly these boards will need to have good isolation of different voltages and current paths.

One of the main points of this project is to be able to test various control algorithms using various architecture. To that end, the inputs and outputs will be well documented so that any processor (Microcontroller, ARM, FPGA, PC, etc) can potentially be used as the master controller.

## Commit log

2012-10-04 Set-up initial files
    [Accel BOM.xlsx]
2012-10-04 Started ring sketchup
    [Full Ring.skp]
2012-10-04 Small further development of sketchup
    [Full Ring.skp]
2012-12-17 Uploading initial prototype
    [Bobbin.skp, Full Ring.skp]
2013-01-01 Updated with newer 15-degree segment prototype with bend.
    [Accel2cuntitledbb.stl, Bobbin.skp]
2013-01-01 Updated Project Log with the most current measurements and notes.
2013-01-06 Began creating version 3 segment prototype
2013-01-06 Started development on Control Board
    [Control Board.sch]
2013-01-06 Started development on Emitter Board
    [Sensor Emitter Board.sch]
2013-01-06 Started development on Phototransistor Board
    [Sensor Phototransistor Board.sch]
2013-01-06 Began updating BOM with most significant components
    [Accel BOM.xlsx]
2013-01-06 Bent the latest segment prototype. Last step is making screw holes.
2013-01-07 Completed Segment prototype 3
    [Accel3.stl]
2013-02-05 Updated with Prototype 4 and more notes
    [Segment.scad, Segment.stl]
2013-02-05 Updated with Prototype 5 and updated notes
    [Accel2cuntitledbb.stl, Accel3.stl, Segment.scad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]
